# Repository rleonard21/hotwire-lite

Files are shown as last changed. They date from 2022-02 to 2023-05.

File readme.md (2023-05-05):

# Hotwire Lite
## Overview
My [original hotwire controller design](https://github.com/rleonard21/hotwire-controller) was my first real embedded systems project and
had several shortcomings as a result. The goal of this "lite" project was to design and build
the cheapest version of the original project while significantly improving its performance.

(The [original project](https://github.com/rleonard21/hotwire-controller/blob/master/README.md) has some nice pictures of the project in action.)

A close up of the v1.0 hardware under test.

## Observations
1. The power, LCD, and PID settings were never changed after finding the
right values.
2. The rotary encoder was a bit delicate when wearing gloves.
3. The circuit was erroneously running at 244Hz PWM and 14Hz PID rates and took several seconds to settle.

## Project Results
#### Product Costs
| Cost (single) | Original Hotwire | Hotwire Lite |
|---|---|---|
| PCB | $5 (ALLPCB) | $5 (PCBWay)  |
| Electrical | ~$38 | $5.18 |
| Mechanical | ~$20 | $0 |
| Total cost | ~$63 | $10.18 |
| Bulk cost  (100)  | ? | $3.71 |
| PCB assembly time | 1-1.5 hours | <20 minutes  |
| Machining time | 2-3 hours | N/A |

#### Ease of Manufacturing
| Manufacturing Ease | Original Hotwire | Hotwire Lite |
|---|---|---|
| # SMD | 33 | 19 |
| # PTH | 8 | 0 |
| Screws | Yes | No |
| Machining required | Yes | No |

#### Circuit Performance
| Performance | Original Hotwire | Hotwire Lite |
|---|---|---|
| Output accuracy @ 25W  | -4.6% | 0.08% |
| Settling time | ~8 seconds | milliseconds |
| PWM frequency | 244Hz | 1024Hz |
| Control loop frequency | 14Hz | 1KHz |
| Calibration | No | Yes |
| Data output | No | Yes |

## Filtering
The PID controller needs to know the average current running through the
wire to effectively control the power output. The output is really a square
wave, so there needs to be some filtering to find the average. The original
controller did this in hardware with an expensive and bulky RC filter network.
The new circuit performs this in a clever manner. Instead of free running the ADC
and measuring the entire signal, the ADC is trigged only on the rising edge of the 
PWM signal. Therefore, the ADC only ever measures the maximum current in the circuit.
Multiplying this number by the duty cycle results in the average current. 
This operation is be performed much faster than the old circuit (1KHz vs. 14Hz).

## Component Optimization
Being the first circuit I ever made, the original controller was
over-engineered a bit. It used expensive components with great specifications,
even if the circuit didn't really need it. The new controller uses the
right components, trading off unused performance for lower cost.

## UART Data Output Format
The circuit continuously streams its current and voltage measurements over UART at a 1MHz buad. 
The format of the data is a comma-separated list formatted like so: `voltage,current,power,duty_cycle`.
The units are `mV,mA,mW,%*1000`.

## Calibration 
### Calibration Interface
The circuit can be calibrated over UART using a very basic, lightweight interface. The user just needs
to send a three character command over the UART interface, which currently runs at 500k buad.

```
C00-C99: calibrate the voltage divider to account for resistor tolerance. C50 is for ideal resistors.
P00-P99: set the power output, where the two digit number is the output in watts (P15 = 15W output).
```
### Resistor Calibration Calculation
The resistor calibration is performed by measuring the true output voltage, reading the measured voltage over UART,
and performing the following calculation:

```c
resistor_divider = vcc_true / vcc_measured / 3
C_value = round(resistor_divider - 2.50, 2) * 100

calibration command = "C{C_value}"
```

Alternatively, manipulate the C value until the controller is outputting the correct power
to the desired accuracy.

#### Calibration Example:
```c
vcc_true = 13.993  // the voltage as measured by the multimeter
vcc_measured = 13.881  // the voltage as output over UART
resistor_divider = 13.993 / 13.881 / 3 = 3.024
C_value = round(3.024 - 2.50, 2) * 100 = 52

calibration command: "C52"
```
## Images
The assembled v1.0 hardware.
The assembled v1.0 hardware.

A close up of the v1.0 hardware under test.
A close up of the v1.0 hardware while testing.

The four revisions of the hotwire controller project.
The four revisions of the hotwire controller project between 2018 (top) and 2022 (bottom).

The calibration station using a high power PCB resistor.
The calibration station using a high power PCB resistor.

## References
[My original hotwire project](https://github.com/rleonard21/hotwire-controller)

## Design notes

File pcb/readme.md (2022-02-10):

# Hardware Design
## Overview
## Versions
### v0.1
The purpose of this version is to validate the ability to implement the
desired algorithm on the ATTiny402, which has limited SRAM and flash memory.
Common parts with pre-existing KiCad symbols were used with little regard
for optimization.

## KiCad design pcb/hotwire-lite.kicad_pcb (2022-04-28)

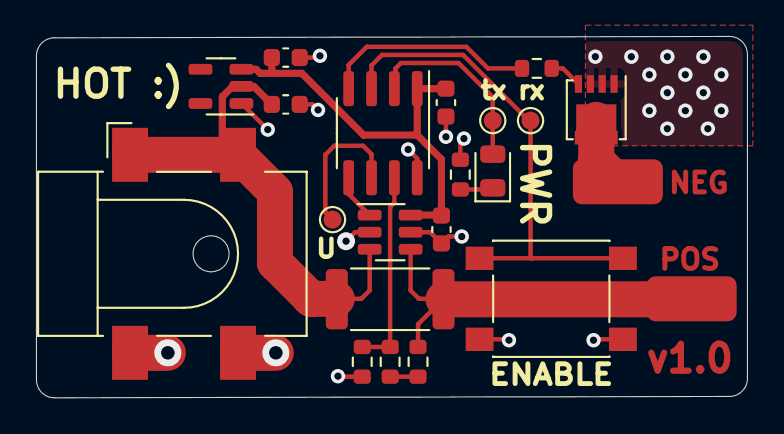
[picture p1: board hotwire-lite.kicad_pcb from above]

Board: 2 copper layers, 39.5 x 20.1 mm, 22 parts (0 on the bottom side), 14 nets.

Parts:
C1, C2: 1uF; C_0603_1608Metric
C3, C4: 0.1uF; C_0603_1608Metric
D1: LED; LED_0805_2012Metric
J1: Barrel_Jack_Switch_Pin3Ring; BarrelJack_CLIFF_FC681465S_SMT_Horizontal
J2: WIRE+; wire_solder_pad
J3: WIRE-; wire_solder_pad
Q1: SiRA18ADP; Vishay_PowerPAK_1212-8_Single
R1, R2, R3: 10k; R_0603_1608Metric
R4, R5: 220; R_0603_1608Metric
R6: 0.050; R_2512_6332Metric
SW1: SW_Push; SW_SPST_PTS645
TP1, TP2, TP3: TestPoint; TestPoint_Pad_D1.0mm
U1: NCP716; SOT-23-5
U2: ATtiny402-SS; SOIC-8_3.9x4.9mm_P1.27mm
U3: INA180A1; SOT-23-6

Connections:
+5V: C2.1, C3.2, C4.2, U1.3 (VOUT), U2.1 (VCC), U3.6 (V+)
/UPDI: TP1.1, U2.6 (~RESET/PA0)
/current_sense: U2.5 (PA2), U3.1
/pwm_output: R5.1, U2.4 (PA1)
/rx_button: SW1.1, TP2.1, U2.3 (PA7)
/tx_led: D1.2 (A), TP3.1, U2.2 (PA6)
/vin: C1.1, J1.1, R6.1, U1.2 (VIN), U3.3 (+)
/voltage_sense: R2.2, R3.1, U2.7 (PA3)
/wire_neg: J3.1, Q1.5 (D)
/wire_pos: J2.1, R1.1, R6.2, U3.4 (-)
GND: C1.2, C2.2, C3.1, C4.1, J1.2, J1.3, Q1.1 (S), Q1.2 (S), Q1.3 (S), R3.2, R4.2, SW1.2, U1.1 (GND), U2.8 (GND), U3.2 (GND), U3.5 (REF)
unnamed: D1.1 (K), R4.1
unnamed: Q1.4 (G), R5.2
unnamed: R1.2, R2.1

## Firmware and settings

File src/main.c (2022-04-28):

/*
 * hotwire-lite.c
 *
 * Created: 2/22/2022 9:34:55 PM
 * Author : Robert
 */ 

#define FIRMWARE_VERSION "v1.0.0"

#define F_CPU 20000000

#include "Init.h"
#include "UART.h"
#include "Debug.h"
#include "ADC.h"
#include "Power.h"
#include "Button.h"
#include "PWM.h"
#include "SysTick.h"
#include "LED.h"
#include "Calibrate.h"
#include "PID.h"

#include <avr/io.h>
#include <util/delay.h>
#include <avr/interrupt.h>

#define DEBUG_MESSAGE "HOTWIRE LITE; DEBUG ENABLED;\r\nFIRMWARE VERSION "

int main(void) {
	
	// initialize peripherals
	Init_clock_setup();
	SysTick_init();
	UART_init(F_CPU);
	
	Calibrate_init();
	ADC_init();
 	Button_init();
	PID_init();
	PWM_init();
	Power_init();
	
	uint8_t debug_mode = Debounce_read() == 1; // return 1 if the button is currently held low

	if(debug_mode) {
		Button_disable();
		UART_enable_tx();
		UART_enable_rx();
		UART_puts(DEBUG_MESSAGE);
		UART_puts(FIRMWARE_VERSION);
		UART_puts("\r\n");
		_delay_ms(1000);
		PWM_start();
	} else {
		LED_init();
	}
	
	sei();
	
	// main application
    while (1) {
		// operate hot wire state based on button
		if(Button_read() && !debug_mode) {
			if(PWM_is_enabled())
				PWM_stop();
			else
				PWM_start();
		}
		
		if(debug_mode) {
			Calibrate_update();
			Power_print_measurements();
		}
	}
		
	return 1;
}

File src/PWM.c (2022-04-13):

/*
 * PWM.c
 *
 * Created: 2/23/2022 9:45:24 PM
 *  Author: Robert
 */ 


#include <stdint.h>
#include <avr/io.h>
#include <avr/interrupt.h>

#include "PWM.h"
#include "LED.h"
#include "Power.h"
#include "PID.h"
#include "Debug.h"
#include "UART.h"

#define PWM_PERIOD	9999

static float duty_cycle_f = 50.0f;
volatile char tick = 0;
const char tick_max = 10;

// EFFECTS: initializes the PWM output
void PWM_init() {
	// set PWM pin to an output
	PWM_PORT.DIRSET = PWM_PIN_bm;
	
	// set the clock divider
	TCA0.SINGLE.CTRLA = TCA_SINGLE_CLKSEL_DIV2_gc;
	
	// enable output on the pin and set the timer to single slope PWM
	TCA0.SINGLE.CTRLB = TCA_SINGLE_CMP1_bm | TCA_SINGLE_WGMODE_SINGLESLOPE_gc;
	
	// set the period of the timer
	TCA0.SINGLE.PER = PWM_PERIOD;
	
	// set the duty cycle of the timer
	PWM_update_duty(0);
	
	// enable the overflow interrupt for triggering the control system
	TCA0.SINGLE.INTCTRL = TCA_SINGLE_OVF_bm;
}

// EFFECTS: starts the PWM output
void PWM_start() {
	TCA0.SINGLE.CTRLB |= TCA_SINGLE_CMP1_bm;
	
	// start the timer
	TCA0.SINGLE.CTRLA |= TCA_SINGLE_ENABLE_bm;
	
	LED_on();
}

// EFFECTS: stops the PWM output
void PWM_stop() {
	PWM_update_duty(0);
	
	// stop the timer
	TCA0.SINGLE.CTRLA &= ~TCA_SINGLE_ENABLE_bm;
	TCA0.SINGLE.CTRLB &= ~TCA_SINGLE_CMP1_bm;
	
	LED_off();
}

// EFFECTS: changes the duty cycle of the PWM
void PWM_update_duty(uint16_t value) {
	TCA0.SINGLE.CMP1 = value;
}

// EFFECTS: updates the duty cycle to a set percentage
void PWM_update_duty_percent(uint8_t percent) {
	duty_cycle_f = (float)(TCA0.SINGLE.PER) / 100.0f;
	TCA0.SINGLE.CMP1 = (uint16_t)(duty_cycle_f * (float)(percent));
}

// EFFECTS: toggles the PWM
void PWM_toggle() {
	TCA0.SINGLE.CTRLA ^= TCA_SINGLE_ENABLE_bm;
}

// EFFECTS: returns 0 if the PWM is currently disabled
uint8_t PWM_is_enabled() {
	return TCA0.SINGLE.CTRLA & TCA_SINGLE_ENABLE_bm;
}

// EFFECTS: returns the duty cycle
float PWM_get_duty_cycle() {
	return (float)(TCA0.SINGLE.CMP1) / (float)(TCA0.SINGLE.PER);
}

// EFFECTS: returns the setting of the PWM timer
uint16_t PWM_get_setting() {
	return TCA0.SINGLE.CMP1;
}

// EFFECTS: changes the overflow value based on the output of the PID controller
void PWM_PID_input(int16_t value) {
	if ((long)(TCA0.SINGLE.CMP1) + (long) (value) >= (long) (TCA0.SINGLE.PER)) {
		TCA0.SINGLE.CMP1 = TCA0.SINGLE.PER - 1;
	} else if ((long) (TCA0.SINGLE.CMP1) + (long) (value) <= 0) {
		TCA0.SINGLE.CMP1 = 0;
	} else {
		TCA0.SINGLE.CMP1 += value;
	}
}

// ISR: executes on the rising edge of the PWM signal
ISR(TCA0_OVF_vect) {
	PID_update_service();

	// clear the flag
	TCA0.SINGLE.INTFLAGS = TCA_SINGLE_OVF_bm;
}

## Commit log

2022-01-31 implemented the skipping average in C
    [main.c]
2022-02-01 added some optimizations, saved about ~150 bytes in compiled size for SA filter
2022-02-02 started v0.1 test hardware
    [hotwire-lite.kicad_pcb, hotwire-lite.sch]
2022-02-10 updated pcb
    [hotwire-lite-B_Cu.gbr, hotwire-lite-B_Mask.gbr, hotwire-lite-B_Paste.gbr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]
2022-04-13 Power measure implementation
    Firmware now successfully measures power and controls output via PID.
2022-04-17 added some printing for v0.1.0
2022-04-19 v0.1.0 files were in wrong directory
    [ADC.c, Button.h, Calibrate.c]
2022-04-19 removed files in wrong spot
    [ADC.c, Button.h, Calibrate.c]
2022-04-19 added new v1.0 hardware design
    [hotwire-lite.kicad_pcb, hotwire-lite.kicad_sch]
2022-04-19 v1.0 hardware
    [hotwire-lite-B_Cu.gbr, hotwire-lite-B_Mask.gbr, hotwire-lite-B_Paste.gbr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]
2022-04-19 exported v1.0 for order
    [hotwire-lite-B_Cu.gbr, hotwire-lite-B_Mask.gbr, hotwire-lite-B_Paste.gbr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]
2022-04-21 EEPROM implementation
    * Added nonvolatile memory saving for calibration and power setting
    * Fixed UART input reliability
    [ADC.c, Calibrate.c, Power.c]
2022-04-21 changed resistor values
    [hotwire-lite.kicad_pcb, hotwire-lite.kicad_sch]
2022-04-28 Updated to v1.0 hardware
    + removed unused code
    + fixed calibration erase on reflash problem
    [ADC.c, Calibrate.c, main.c]
